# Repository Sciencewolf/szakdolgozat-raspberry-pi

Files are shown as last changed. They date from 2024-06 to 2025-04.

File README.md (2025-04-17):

# Szakdolgozat Raspberry Pi(Hardware) part

> [!IMPORTANT]
>  - First Hatching started at 2025-02-21 18:07:59 
>  - Hatching ended at 2025-03-15 15:30:16
>  - Result: 0 kikelés

> [!IMPORTANT]
>  - Second Hatching started at 2025-03-24 17:46:28
>  - Hatching ended at 2025-04-15 10:55:33
>  - Result: 0 kikelés, 2 viszont fejlődött

> [!NOTE]
> LED Color Code

- Lid open: red
- Heating element on: green
- Cooler on: white
- DC motor on: yellow
- Raspi on: cold white
- Other: -

# Preparing



# Hardware Wiring

## All Hardware

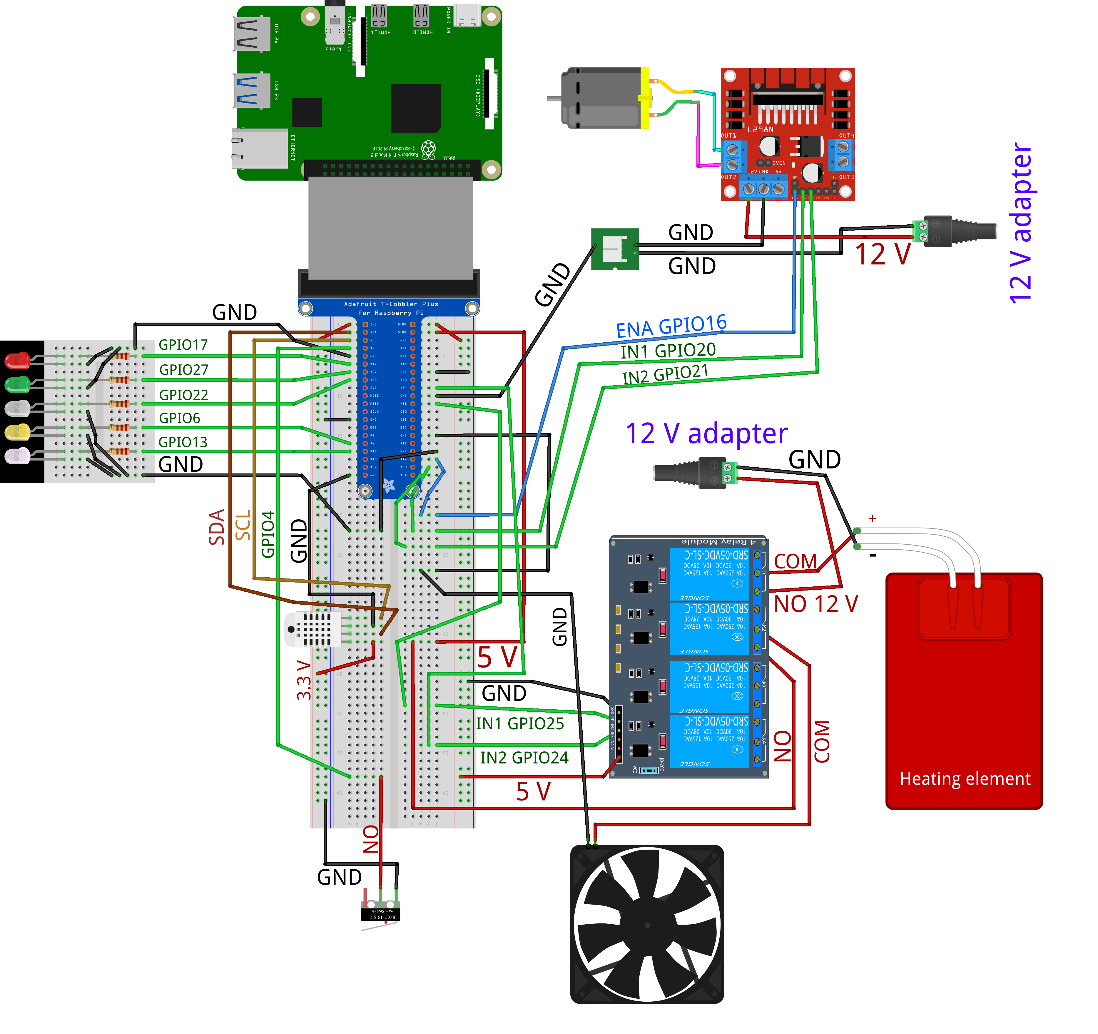
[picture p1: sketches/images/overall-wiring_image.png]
all hardware wiring image


## Hardware with Relay

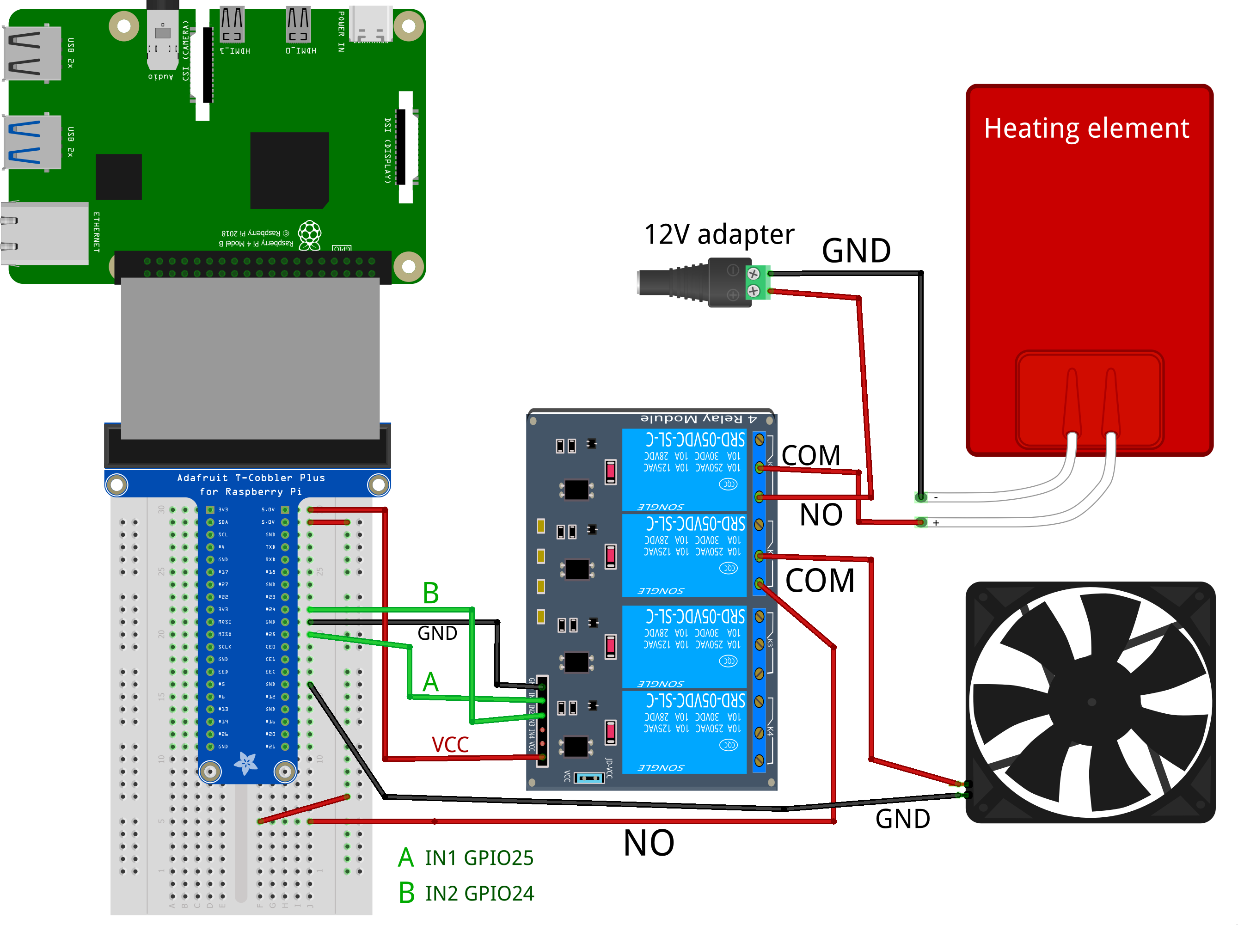
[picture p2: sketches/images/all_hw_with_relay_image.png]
all hw with relay


## AHT20 wiring

> [!NOTE]
> Required hardware

- Raspberry Pi 4 model B
- Breadboard
- Adafruit T-Cobbler
- 1x Adafruit AHT20 Temperature and Humidity Sensor
- 4x Male-Male Wire

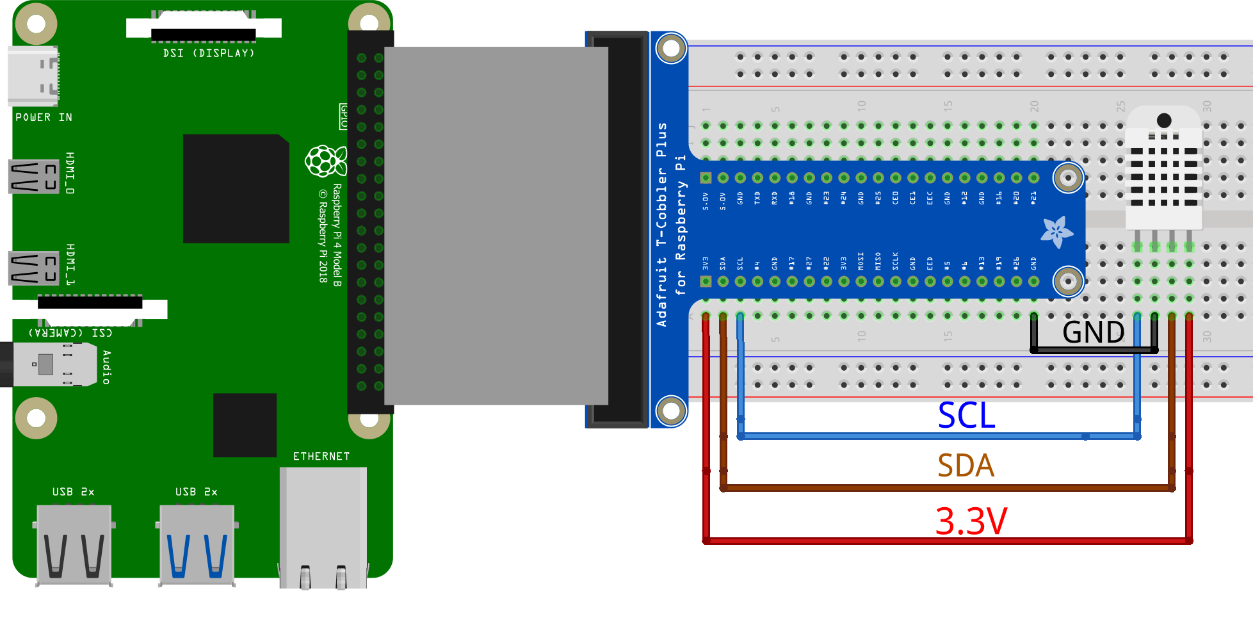
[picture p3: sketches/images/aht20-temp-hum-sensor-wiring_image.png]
AHT20 wiring


## Limit Switch wiring

> [!NOTE]
> Required hardware

- Raspberry Pi 4 model B
- 1x V-156-1C25 Limit Switch
- 2x Male-Female Wire

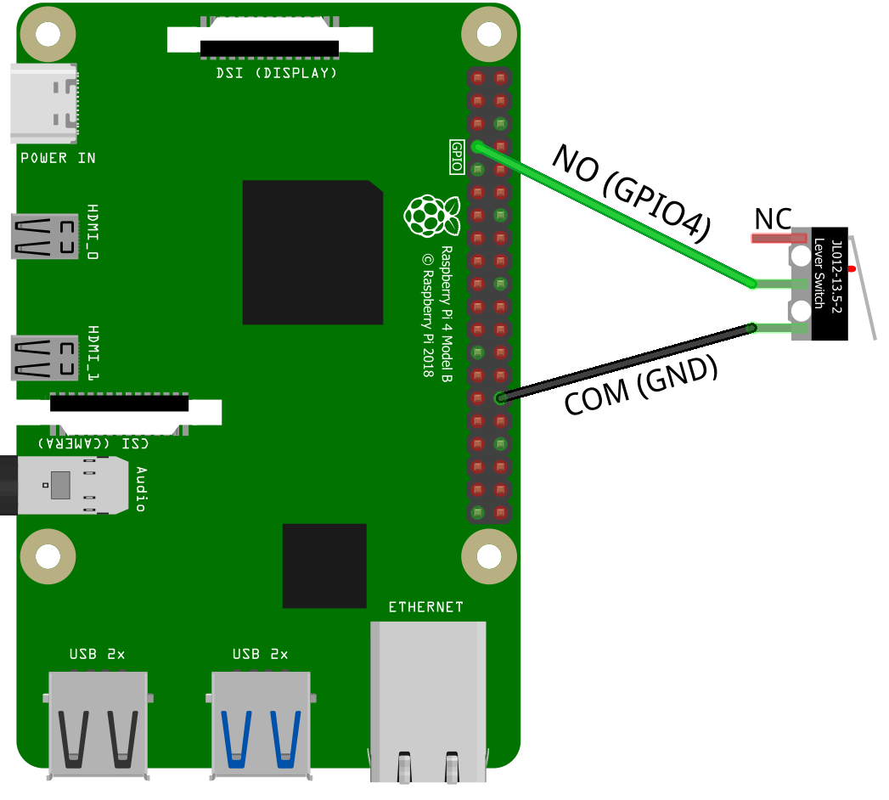
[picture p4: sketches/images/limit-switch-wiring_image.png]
V-156-1C25 Limit Switch wiring


## Fan with Relay wiring

> [!NOTE]
> Required hardware

- Raspberry Pi 4 model B
- Breadboard
- Adafruit T-Cobbler (or, connect directly to ras-pi)
- 1x 5V Fan
- 1x Relay (4 relay module)
- 6x Male-Male wire

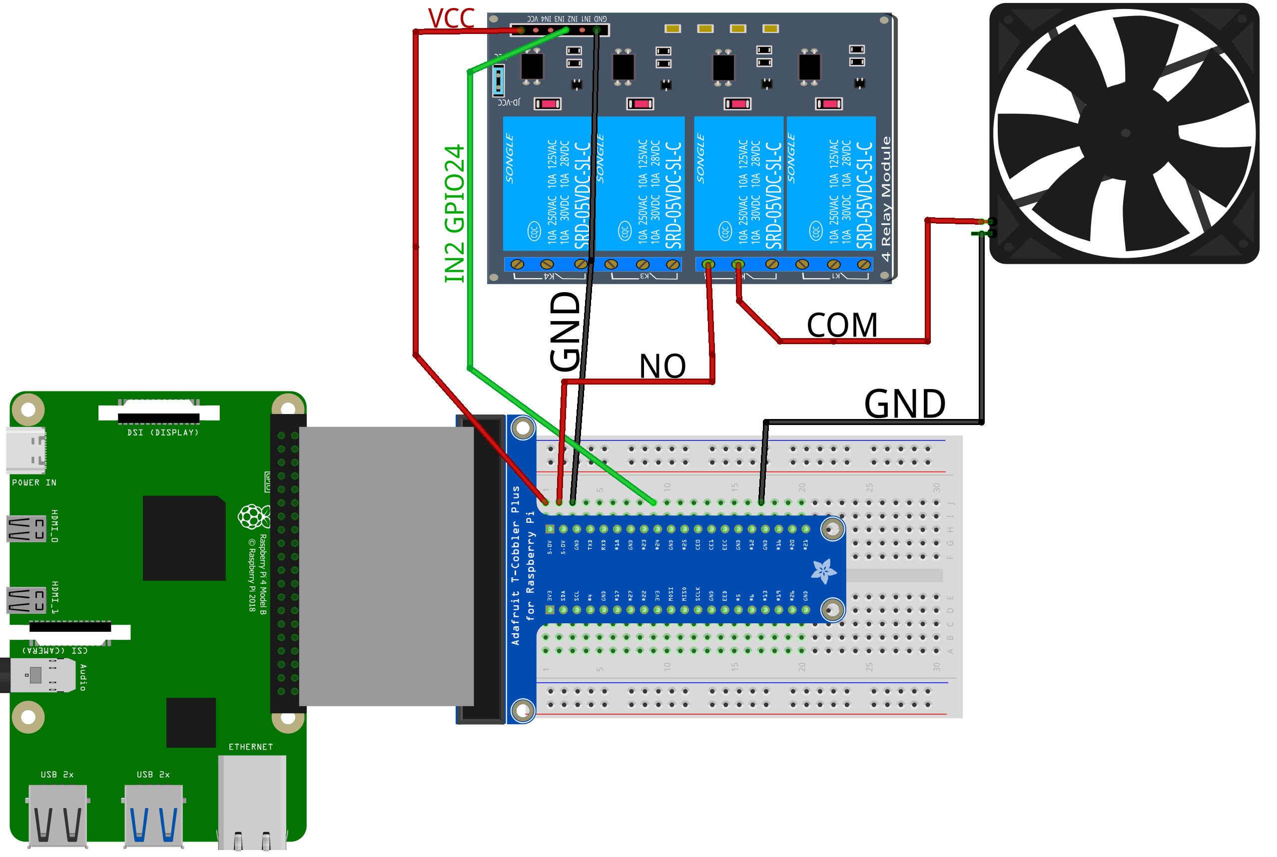
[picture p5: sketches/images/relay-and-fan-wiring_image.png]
Fan with Relay wiring


## Heating Element with Relay wiring

> [!NOTE]
> Required hardware

- Raspberry Pi 4 model B
- Breadboard
- Adafruit T-Cobbler (or, connect directly to ras-pi)
- 1x Heating Element (12V, 110℃)
- 1x 12V Adapter (12V*2A)
- 1x Relay (4 relay module)
- 4x Male-Male Wire

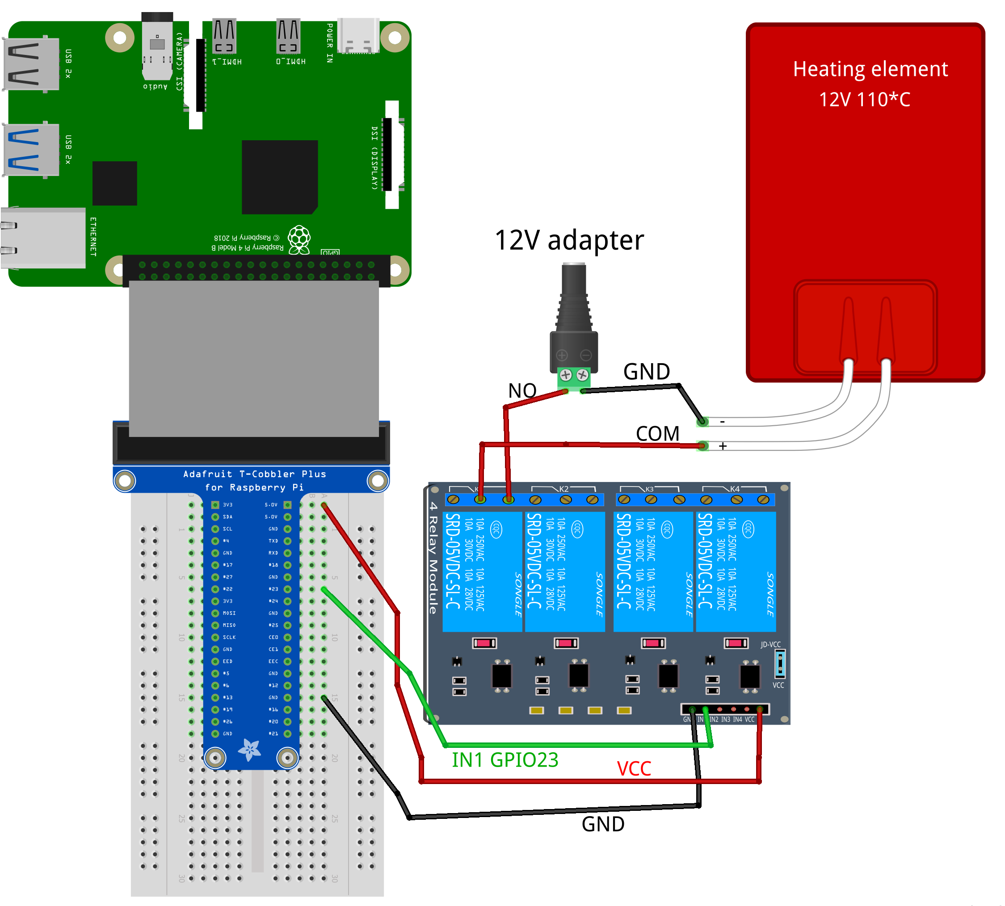
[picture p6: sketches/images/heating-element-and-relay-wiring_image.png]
Heating Element with Relay wiring


## DC Engine wiring

> [!NOTE]
> Required hardware

- Raspberry Pi 4 model B
- Breadboard
- Adafruit T-Cobbler (or, connect directly to ras-pi)
- 1x DC Engine (12V, 75RPM)
- 1x 12V Adapter (12V*1A)
- 1x L298N Dual H-Bridge Motor Driver
- 8x Wire

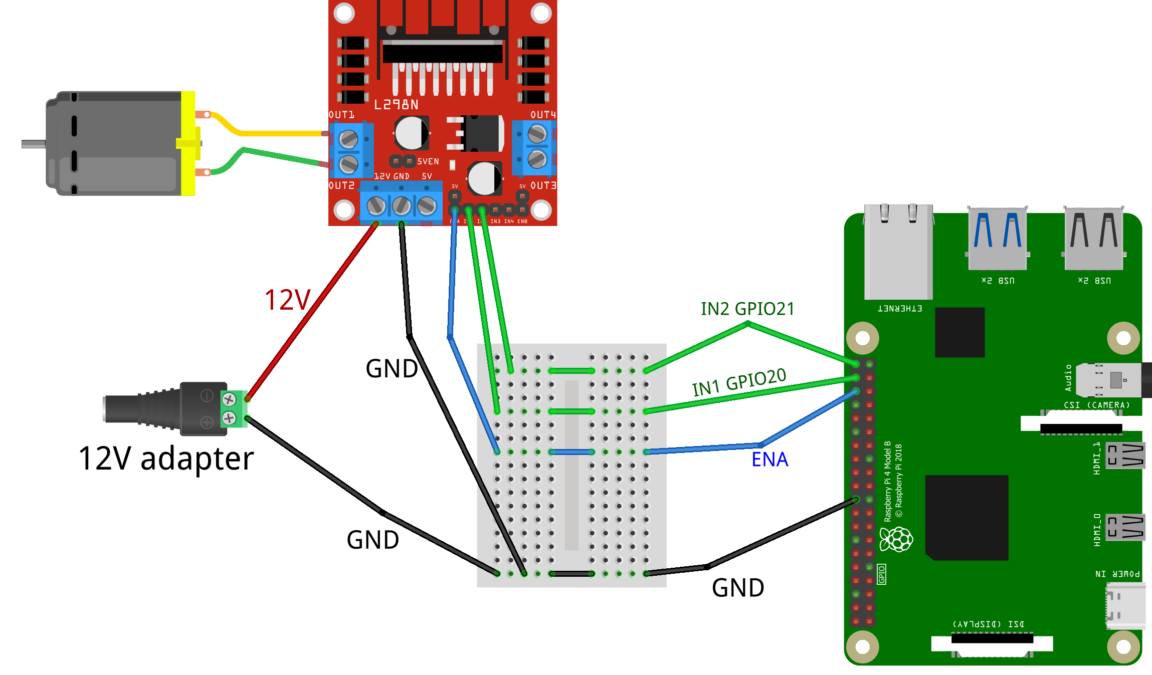
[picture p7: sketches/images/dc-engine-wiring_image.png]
DC Engine wiring


## LED Panel wiring

> [!NOTE]
> Required hardware

- Raspberry Pi 4 model B
- Breadboard
- Adafruit T-Cobbler (or, connect directly to ras-pi)
- 5 LED (Red, Green, White, Yellow, Cold White)
- 7x Wire

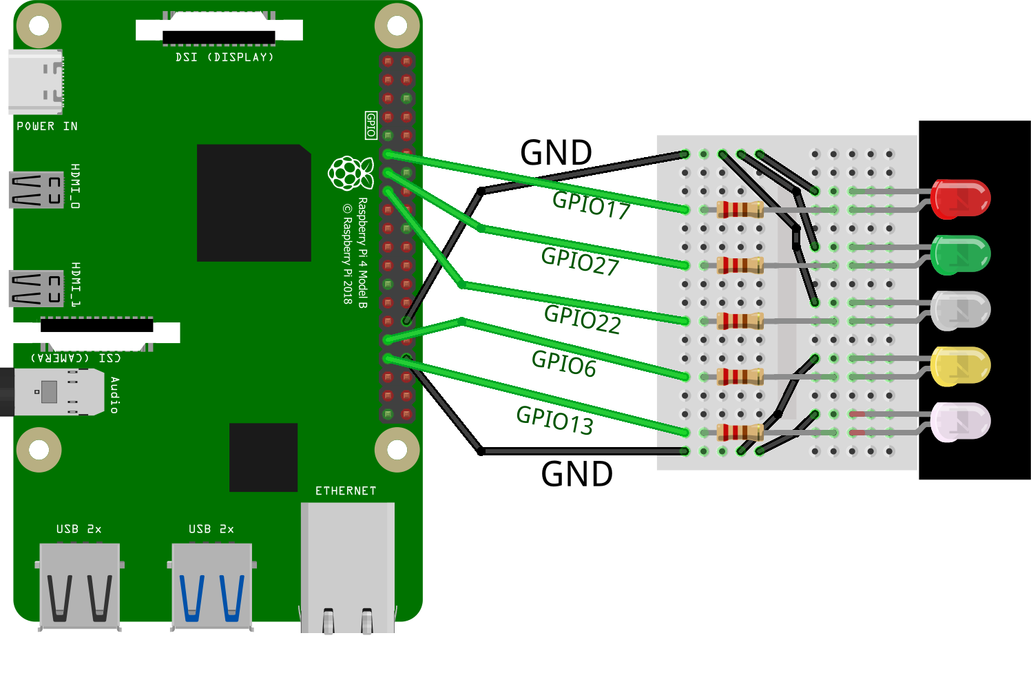
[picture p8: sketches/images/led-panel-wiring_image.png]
LED Panel wiring


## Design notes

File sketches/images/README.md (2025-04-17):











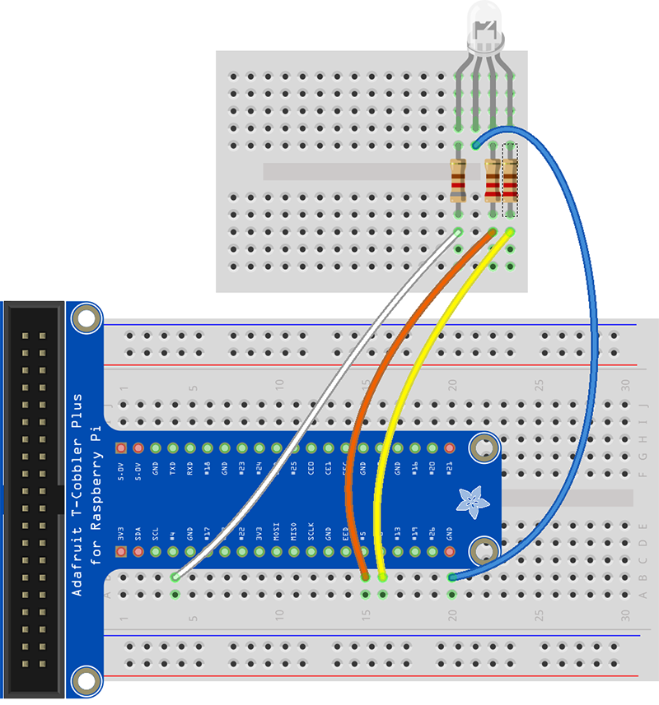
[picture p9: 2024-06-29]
static/images/RGBLedGPIO.webp

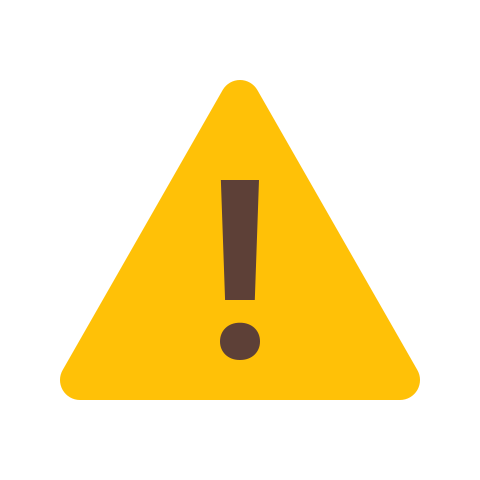
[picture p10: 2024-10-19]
static/images/error.png

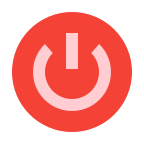
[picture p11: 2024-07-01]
static/images/shutdown.png

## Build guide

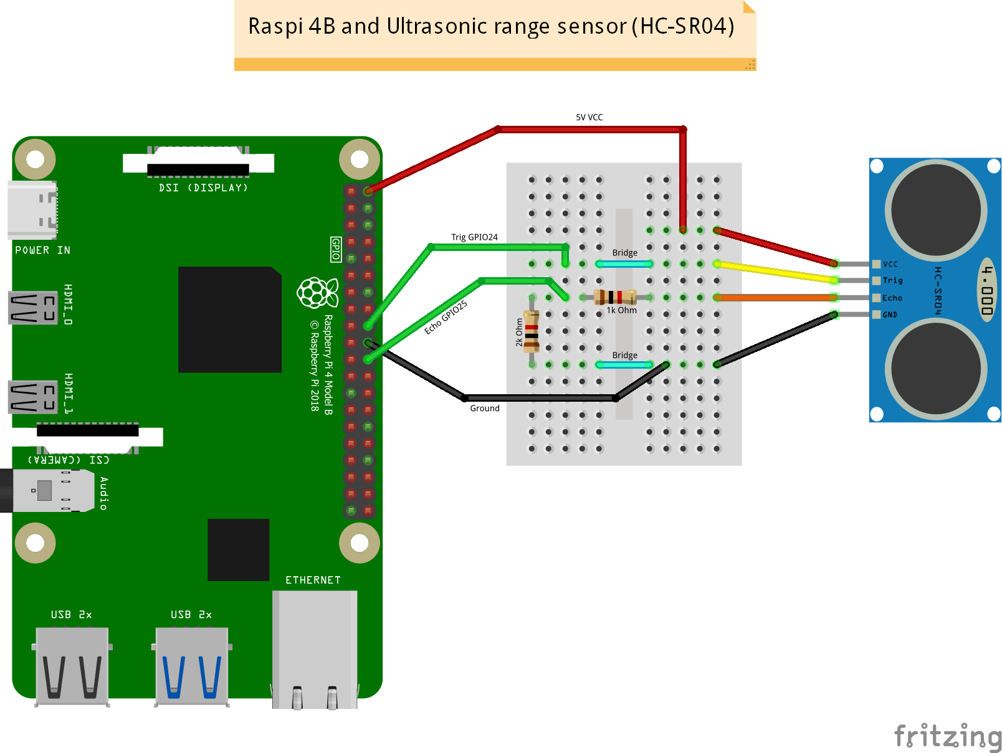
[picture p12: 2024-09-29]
sketches/images/ultrasonic-range-sensor-wiring_image.png

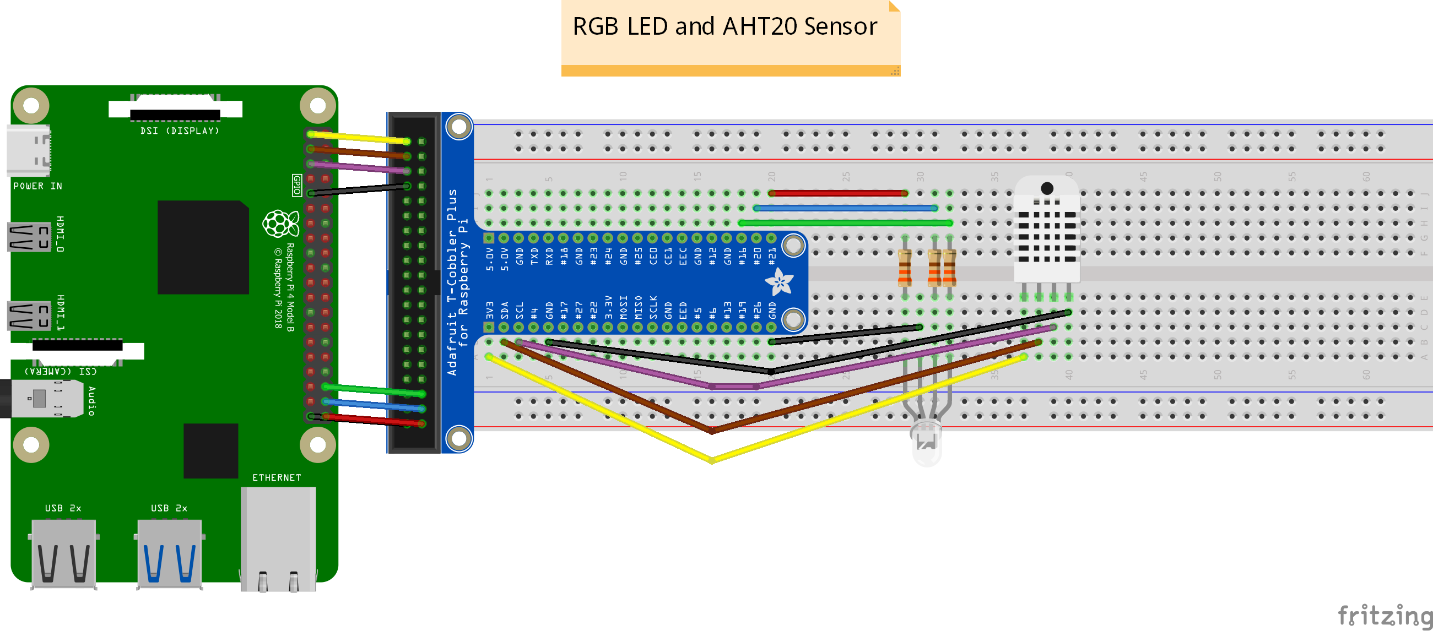
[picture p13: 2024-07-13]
sketches/images/rgb-led-aht20-temp-hum-sensor-wiring_image.png

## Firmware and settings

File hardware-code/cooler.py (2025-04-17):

#!/usr/bin/env python3

"""
wiring: https://github.com/Sciencewolf/szakdolgozat-raspberry-pi/blob/main/sketches/images/relay-and-fan-wiring_image.png
"""

import RPi.GPIO as gpio
from signal import signal, SIGTERM, SIGHUP
import time
from csibekelteto_utils import RELAY_PINS

RELAY_GPIO_PIN: int = RELAY_PINS.get('cooler')

gpio.setmode(gpio.BCM)
gpio.setup(RELAY_GPIO_PIN, gpio.OUT)

def main():
    try:
        signal(SIGTERM, safe_exit)
        signal(SIGHUP, safe_exit)

        gpio.output(RELAY_GPIO_PIN, gpio.LOW)

        while True:
            time.sleep(1)
    except Exception as e:
        print(f"Error: {e}")
    finally:
        gpio.output(RELAY_GPIO_PIN, gpio.HIGH)
        gpio.cleanup()



def safe_exit(signum, frame) -> None:
    """ Provides a safe shutdown of the program """
    exit(1)


if __name__ == "__main__":
    main()

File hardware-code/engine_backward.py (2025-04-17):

#!/usr/bin/env python

"""
wiring: https://github.com/Sciencewolf/szakdolgozat-raspberry-pi/blob/main/sketches/images/dc-engine-wiring_image.png
"""

import RPi.GPIO as gpio
from signal import signal, SIGTERM, SIGHUP
import time

ENA_GPIO_PIN: int = 16
IN1_GPIO_PIN: int = 20
IN2_GPIO_PIN: int = 21

gpio.setmode(gpio.BCM)

gpio.setup(IN1_GPIO_PIN, gpio.OUT, initial=gpio.LOW)
gpio.setup(IN2_GPIO_PIN, gpio.OUT, initial=gpio.LOW)
gpio.setup(ENA_GPIO_PIN, gpio.OUT, initial=gpio.LOW)

pwm = gpio.PWM(ENA_GPIO_PIN, 100)  # 100Hz PWM
pwm.start(0)


def main():
    try:
        signal(SIGTERM, safe_exit)
        signal(SIGHUP, safe_exit)

        pwm.ChangeDutyCycle(0)
        time.sleep(0.5)

        gpio.output(IN1_GPIO_PIN, gpio.HIGH)
        gpio.output(IN2_GPIO_PIN, gpio.LOW)
        pwm.ChangeDutyCycle(20)  # 20% speed

        while True:
            time.sleep(1)
    except Exception as ex:
        print("Exiting...", ex.__str__())
    finally:
        pwm.stop()
        gpio.cleanup()



def safe_exit(signum, frame) -> None:
    """ Provides a safe shutdown of the program """
    exit(1)


if __name__ == "__main__":
    main()

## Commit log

2024-06-28 feat: first test of rpi with blink a led
2024-06-28 feat: custom logger for szakdolgozat-raspberry-pi project
2024-06-29 blink red green or blue led
2024-06-29 test: trying to use temp and hum sensor
2024-06-30 test: add red led command to turn on from webserver
2024-06-30 feat: add control red led on off
2024-06-30 feat: add command for all rgb leds
2024-06-30 feat: ui changes, all rgb led on/off command
2024-06-30 feat: read temp and hum from sensor
2024-06-30 feat: temp and hum sensor control
2024-06-30 test: testing temp hum sensor reading
2024-06-30 fix: issue with displaying data
    [temp_hum_sensor.py]
2024-06-30 fix: issue with reading sensor is fixed
    [temp_hum_sensor.py]
2024-06-30 feat: detect sensor when in usage by led turning on
2024-07-02 feat: removed shutdown button
2024-07-02 style: on/off switch added
2024-07-03 fix: issue with logging
    [temp_hum_sensor.py]
2024-07-03 fix: issue with logging #2
    [rgb-led.py, temp_hum_sensor.py]
2024-07-03 fix: issue with logging and running script
    [rgb-led.py]
2024-07-07 feat: LED's migrated to another GPIO's
2024-07-13 docs: add sketches, update README file
    [rgb-led-aht20-temp-hum-sensor-wiring.fzz]
2024-09-10 fix: issue with indicating raspi on
    [indicate_raspi_on.py]
2024-09-26 test: testing switch
2024-09-26 feat: limit switch is working now
2024-09-26 fix: issue with reading data
    [switch.py]
2024-09-26 fix: issue with webserver and switch code
    [switch.py]
2024-09-26 fix: issue with path
    [switch.py]
2024-09-26 api: use limit switch
2024-09-29 test: testing ultrasonic range sensor
2024-09-29 feat: add images
    [limit-switch-wiring.fzz, ultrasonic-range-sensor-wiring.fzz]
2024-09-30 fix: webserver lid file path #2
    [switch.py]
2024-09-30 fix: webserver lid file path #3
    [switch.py]
2024-09-30 fix: issue with lid path
    [switch.py]
2024-10-01 test: cooler with relay
2024-10-01 test: cooler with relay #2
2024-10-01 feat: cooler with relay is now working
2024-10-01 docs: add fan with relay wiring images and docs
    [relay-and-fan-wiring.fzz]
2024-10-13 test: testing heating element with relay and raspi
2024-10-16 image: add sketch images
    [heating-element-and-relay-wiring.fzz]
2024-10-16 refactor: images and sketches moved into separate files
    [heating-element-and-relay-wiring.fzz, limit-switch-wiring.fzz, relay-and-fan-wiring.fzz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]
2024-10-17 fix: time.sleep in heating element
    [heating_element.py]
2024-10-17 fix#2: typo in heating element
    [heating_element.py]
2024-10-17 test(ui)#1: new version, heating element on/off
2024-11-16 test: new api endpoint and csibekelteto system
    [overall-wiring.fzz]
2024-11-17 frontend: add icons for led's
2024-11-19 fix: cooler and heating element is set to LOW signal
    [cooler.py, heating_element.py, raspi-blinka.py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]
2024-11-22 feat: dc motor is ready
2024-11-22 feat: new api endpoint, yellow led added, dc_motor.py refactoring
2024-11-22 feat: add ui for dc motor
2024-11-23 fix: typo in led filenames
2024-11-23 feat: api endpoints for dc motor
2024-11-23 test(ui): dc motor actions
2024-11-23 fix: dc motor direction
    [dc_motor_backward.py, dc_motor_forward.py]
2024-11-23 fix: dc motor buttons
2024-11-23 feat: added yellow led indication when dc motor is on
2024-11-23 test: dc motor and yellow led working together
2024-11-23 test#2: dc motor and yellow led together, issue with stop process
2024-11-24 test: blue led written with gpiozero package
2024-11-24 test: migration from RPi.GPIO to gpiozero for led
2024-11-25 Revert "chmod added"
    This reverts commit 446fa2cfc2b8123e197d2416872c80154d52b04e.
    [blink_blue_led.py, blink_red_led.py]
2024-11-25 Revert "refactor: safe_exit moved into utils class"
    This reverts commit dacad1667b57ecd06c44f53ce40b7eb4a3207d6e.
    [blink_blue_led.py, blink_red_led.py, cooler.py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]
2024-11-25 chmod added for led's
2024-11-27 test: new led colors
2024-11-27 test(ui): new led buttons
2024-11-27 feat(api, ui): new api endpoins for led, ui fix
    [dc_motor_backward.py, dc_motor_forward.py]
2024-11-27 gpio pin updated
2024-11-27 test: universal file for led
2024-11-27 test#2: universal file for led
2024-11-27 fix: led file path
    [led.py]
2024-11-27 feat: for LED's is now only one file
2024-11-28 refactor, test(humidifier): start and stop process methods, test humidifier with relay
2024-11-28 fix: fixed issue with countdown
    [humidifier.py]
2024-11-28 feat: added humidifier method, led methods updated
2024-12-12 added help for led file if 0 args passed
2025-01-09 feat: purple led replaced for cold white led, preparing features to set temp and hum
2025-01-10 fix(hardware-code): fixed issue with cpu overloading
    [cooler.py, dc_motor_backward.py, dc_motor_forward.py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]
2025-01-10 refactor: indicate raspi on is now cold white led
2025-01-10 fix: issue with temp hum sensor file
    [temp_hum_sensor.py]
2025-01-19 fix: issue with cooler and switch
    [cooler.py, switch.py]
2025-01-21 refactor: lid and temphum sensor files is refactored
2025-02-05 feat: orange LED is removed hw and code also
2025-02-18 feat: added fade in/out effect for led
2025-02-19 feat: added start, prepare and stop hatching function with api, led is not working at night
2025-02-20 feat: hatching started, bug fixed
    [engine_backward.py, engine_forward.py]
2025-02-21 fix(hw, api): issue with heating element, relay and code
2025-02-21 feat: added script to filter data for android app
2025-02-22 fix: issue with heating element turning off loop
2025-02-24 refactor: normal temperature range updated
2025-02-26 fix: issue with relay when heating element is turning on/off
2025-02-26 fix: issue with relay now triggers only once
2025-03-15 added filter_stats file
2025-03-20 test: new version, humidifier removed
    [heating-element-and-relay-wiring.fzz, rgb-led-aht20-temp-hum-sensor-wiring.fzz]
2025-03-26 filter stats every day at last minute
